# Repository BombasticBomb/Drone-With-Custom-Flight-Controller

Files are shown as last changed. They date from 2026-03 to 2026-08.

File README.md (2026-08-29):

## Custom Drone Flight Controller
Arduino + MPU9250 based Flight Controller for Quadcopter!
This project is a custom-built quadcopter drone that uses an Arduino flight controller with an MPU9250 IMU. Will use a flight controller written in Arduino C++ with a cascaded PID loop for stabilization!

## Build Journal Log
Link: https://github.com/BombasticBomb/Custom-Flight-Controller-Quadcopter-With-RaspberryPI-Cam/blob/main/JOURNAL.md

## 3D Model

This'll be printed in Carbon Fiber Nylon Filament, so it is actually strong enough to be a drone chassis. I will also use a Gyroid infill pattern with 40% infill to make it really strong, and I'll also use a wall count of 6 for further reinforcement. 
parts

## Inspiration
This is my hack club project to build a quadcopter from scratch with a custom flight controller with Arduino &amp; MPU9250. Growing up, I'd watch many science and engineering videos online; I've always been a science kid who spends his time watching astronomy, engineering, etc type videos. I did this project to challenge myself in learning the ins and outs of how a quadcopter actually works, and also to combine my skills in hardware, electronics, and coding to create something unique and not just follow a tutorial.


 ## What Makes This Project Unique
Unlike most custom drones that rely on preprogrammed ready-to-fly flight controllers, my project uses a fully custom flight controller using Arduino & mpu9250 that I had to do a lot of research to actually learn how it works using custom cascaded PID controller loops (and in the future, an extended Kalman filter), and I am working on developing it into a fully functioning firmware. Along with that, I am utilizing a novel method to stream video transmission using a USB camera and the Raspberry Pi using a Python script that uses OpenCV to play video on a web dashboard hosted in Flask and streamed with Flask-socketio. This is a unique method as I offload the low-level control to the Arduino, while I implement advanced features such as a camera (and hopefully in the future GPS, ultrasonic sensors, etc) through the more powerful Raspberry Pi, which actually runs the Linux Operating System.
- Arduino --> Does the low-level flight control and sensor fusion
- Raspberry Pi --> Video Streaming
**Note: Using the onboard wifi on the Raspberry Pi does mean the video transmission range is limited, and beyond that range, we have to rely solely on radio.

## Wiring Diagrams
circuit diagram


| # | Arduino --> MPU9250 | | |
| - | --- | - | --- |
| | **Arduino** | --> | **MPU9250** |
| | 5V | --> | 5V |
| | GND | --> | GND |
| | A4 | --> | SDA |
| | A5 | --> | SCL |

| # | Arduino --> RC Receiver | | |
| - | --- | - | --- |
| | **Arduino** | --> | **RC Receiver** |
| | 5V | --> | 5V |
| | GND | --> | GND |
| | RX | --> | IBus |

| # | Arduino --> ESC | | |
| - | --- | - | --- |
| | **Arduino** | --> | **ESC** |
| | 5V | --> | 5V |
| | GND | --> | GND |
| | 3 | --> | ESC1 |
| | 4 | --> | ESC2 |
| | 5 | --> | ESC3 |
| | 6 | --> | ESC4 |

## Custom PCB:

pcb
Note: The ESCs themselves are part of the wiring diagram and are powered by the Arduino. It is crucial to note the motors themselves, and the Arduino also gets power from the main battery. The reason this configuration was required is that the Arduino converts the 11.1V on the 3S battery to 5V and supplies it to the other electronics.

# Bill of Materials

| Name | Purpose | Quantity | Total Cost (USD) | Link | Distributor |
|---|---|---|---|---|---|
| EVE 50PL 21700 5000mAh 50A Battery | This'll power the drone through its flight. I decided to buy Li-ion batteries and manually connect 3 to make a 3S cell to make a 5000mAh 3S battery pack. This'll help the drone fly longer. I'm buying one extra just in case. | 4 | 24.00 | https://www.18650batterystore.com/products/eve-50pl-21700-5000mah-50a-battery?variant=46405896798359 | 18650 Battery Store |
| JLCPCB Order + Shipping | I'll be manufacturing my custom PCB from JLCPCB. | 1 | 4.30 | https://cart.jlcpcb.com/quote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 | JLCPCB |
| Male & Female Headers | It'll be used to connect things on the PCB. | 1 | 3.82 | https://www.aliexpress.us/item/3256805860047704.html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 | AliExpress |
| XT90 Male to XT60 Female connector for battery | This converts the XT90 on the battery to XT60 so it can be connected to the PCB. | 1 | 1.00 | https://www.aliexpress.us/item/3256809870073827.html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 | AliExpress |
| Drone Frame | This will be the frame that I will be doing all the testing on. I'll have to ship it to my location. | 1 | 5.00 | https://github.com/hackclub/print-legion | Hack Club Legion |
| 1400KV Brushless Motors | These will be the motors that generate lift for the drone. | 4 | 33.40 | https://www.robotshop.com/products/e-s-motor-xxd-a2212-brushless-motor-160w-mounting-base-kits-kv-1400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 | Robotshop |
| Raspberry PI 4 4GB | This will be used to connect the USB camera and for video transmission. I already have this, so I will not need to buy it. | 1 | 0.00 | https://www.centralcomputer.com/raspberry-pi-4-model-b-rpi4-modbp-4gb-4gb-ddr4-ram-bcm2711-soc-usb-3-0-poe-enabled.html | Central Computers |
| Arduino Nano | This will be running the flight software and controlling the motors. I already have this, so I will not need to buy it. | 1 | 0.00 | https://www.aliexpress.us/item/3256809956121978.html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 | AliExpress |
| GY-91 Board with both MPU-9250 & BMP180 | This will the the 9 Axis Flight Controller for the drone (Gyroscope, Accelerometer, Magnetometer, Altometer). | 1 | 6.34 | https://www.aliexpress.us/item/3256810419378175.html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 | AliExpress |
| 8x4.5 Inch RC Drone Propellers | These will be used on the brushless motors to provide lift for the drone. I am buying 8 pieces instead of 4 in case some break during testing. | 1 | 0.92 | https://www.aliexpress.us/item/2251832730802090.html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 | AliExpress |
| 3S Li-po Battery Charger US Plug | This will be used to charge the battery. | 1 | 11.61 | https://www.aliexpress.us/item/3256805934795867.html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 | AliExpress |
| MicroZone MC6C Mini V2 2.4G 6CH Controller Transmitter w/ Receiver | This will be used for the radio communication with the drone. | 1 | 35.24 | https://www.aliexpress.us/item/3256807243819244.html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 | AliExpress |
| 30A Brushless Motor ESC | This will be the Electronic Speed Controller for the 4 brushless motors on the drone. I need to buy 2 pieces for a total of 4 for each motor. | 1 | 12.87 | https://www.aliexpress.us/item/2252799818726193.html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 | AliExpress |
| 12V-5V Buck Converter | This'll convert the 11.1V from the 21700 battery pack to 5V so the Raspberry PI can use it. | 1 | 0.99 | https://www.aliexpress.us/item/3256806059787124.html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 | AliExpress |
| **Total** | | | **139.49** | | |

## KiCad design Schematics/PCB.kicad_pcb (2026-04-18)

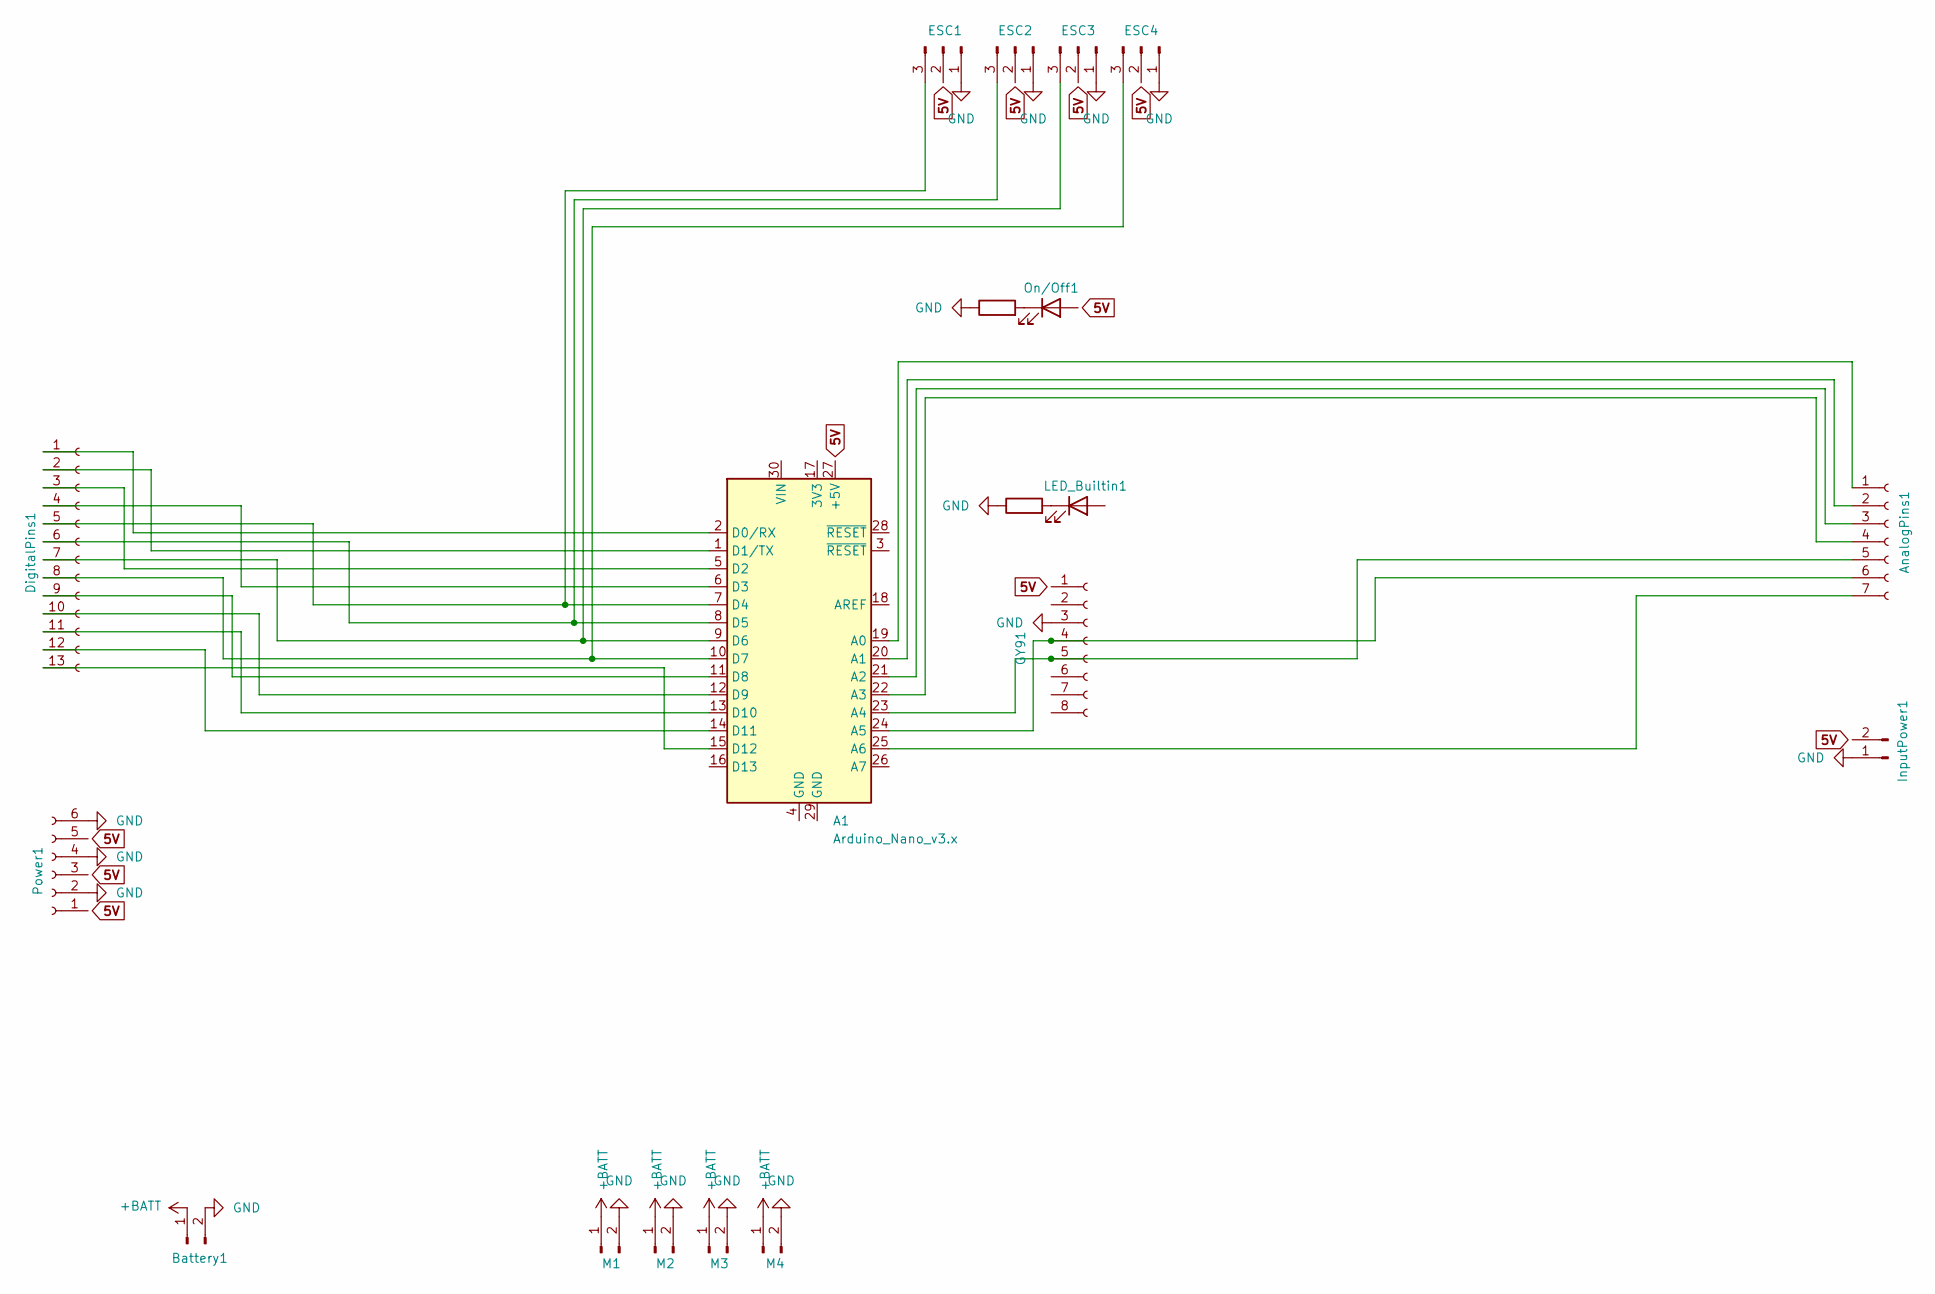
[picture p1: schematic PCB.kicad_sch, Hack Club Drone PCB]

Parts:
A1: Arduino_Nano_v3.x; Arduino_Nano
AnalogPins1: Conn_01x07_Socket; PinSocket_1x07_P2.54mm_Vertical
Battery1: Conn_01x02_Pin; AMASS_XT60PW-M_1x02_P7.20mm_Horizontal
DigitalPins1: Conn_01x13_Socket; PinSocket_1x13_P2.54mm_Vertical
ESC1, ESC2, ESC3, ESC4: Conn_01x03_Pin; PinSocket_1x03_P2.54mm_Vertical
GY91: Conn_01x08_Socket; PinSocket_1x08_P2.54mm_Vertical
InputPower1: Conn_01x02_Pin; PinSocket_1x02_P2.54mm_Vertical
LED_Builtin1: LED; LED_D5.0mm
M1, M2, M3, M4: Conn_01x02_Pin; AMASS_XT60PW-M_1x02_P7.20mm_Horizontal
On/Off1: ON/OFF; LED_D5.0mm
Power1: Conn_01x06_Socket; PinSocket_1x06_P2.54mm_Vertical
R220-1, R220-2: 220; R_Axial_DIN0207_L6.3mm_D2.5mm_P10.16mm_Horizontal

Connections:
+BATT: Battery1.1, M1.1, M2.1, M3.1, M4.1
GND: Battery1.2, ESC1.1, ESC2.1, ESC3.1, ESC4.1, GY91.3, InputPower1.1, M1.2, M2.2, M3.2, M4.2, Power1.2, Power1.4, Power1.6, R220-1.1, R220-2.1
unnamed: A1.19 (A0), AnalogPins1.1
unnamed: A1.20 (A1), AnalogPins1.2
unnamed: A1.21 (A2), AnalogPins1.3
unnamed: A1.22 (A3), AnalogPins1.4
unnamed: A1.23 (A4), AnalogPins1.5, GY91.5
unnamed: A1.24 (A5), AnalogPins1.6, GY91.4
unnamed: A1.25 (A6), AnalogPins1.7
unnamed: A1.2 (D0/RX), DigitalPins1.1
unnamed: A1.1 (D1/TX), DigitalPins1.2
unnamed: A1.5 (D2), DigitalPins1.3
unnamed: A1.6 (D3), DigitalPins1.4
unnamed: A1.7 (D4), DigitalPins1.5, ESC1.3
unnamed: A1.8 (D5), DigitalPins1.6, ESC2.3
unnamed: A1.9 (D6), DigitalPins1.7, ESC3.3
unnamed: A1.10 (D7), DigitalPins1.8, ESC4.3
unnamed: A1.11 (D8), DigitalPins1.9
unnamed: A1.12 (D9), DigitalPins1.10
unnamed: A1.13 (D10), DigitalPins1.11
unnamed: A1.14 (D11), DigitalPins1.12
unnamed: A1.15 (D12), DigitalPins1.13
unnamed: LED_Builtin1.1 (K), R220-2.2
unnamed: On/Off1.1 (K), R220-1.2

Board: 2 copper layers, 19 parts (0 on the bottom side), 24 nets, no tracks yet.

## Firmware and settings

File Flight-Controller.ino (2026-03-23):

// NOTE:
// This is early-stage development of the flight controller.
// Due to lack of physical hardware testing, motor control and PID tuning
// are not finalized yet. Current functionality just focuses on sensor fusion from a mpu6050 which I own for testing purposes, and will switch to a mpu9250 when I get to buy the actual sensor.
// It's the concept and engineering method that is being laid down right now, and it may change or be reimplemented as I build the drone.


#include <SPI.h>
#include <Wire.h>
#include <MPU6050.h>

//MPU
MPU6050 mpu; //I am using mpu6050 cause I have that with me so I can test with it. After I recieve my mpu9250, I'll update the code to use that. 

bool initialized = false;

// Timing
unsigned long prevTime = 0;
unsigned long lastDisplay = 0;

// Angles
float roll = 0;
float pitch = 0;
float yaw = 0;

// Accel angles
float accel_roll = 0;
float accel_pitch = 0;

//Motor libraries
#include <Servo.h>
#include <IBusBM.h>

//Define 4 motors
Servo motor1;
Servo motor2;
Servo motor3;
Servo motor4;

//Define bus for radio communication
IBusBM iBus;

//Flight state
bool flight = false;
int motor1_speed = 0;
int motor2_speed = 0;
int motor3_speed = 0;
int motor4_speed = 0;

void setup() {
  Serial.begin(115200);

  while (!mpu.begin(MPU6050_SCALE_2000DPS, MPU6050_RANGE_8G)) { //2000 degrees and 8G
    Serial.println("Sensor not found!");
    delay(500);
  }
  mpu.setDLPFMode(MPU6050_DLPF_4); 

  // Gyro calibration
  mpu.calibrateGyro();
  mpu.setThreshold(0);

  prevTime = millis();

  iBus.begin(Serial);
  
  //Connect wires (pin 3,4,5,6)
  motor1.attach(3);
  motor2.attach(4);
  motor3.attach(5);
  motor4.attach(6);

  //Ground drone
  ground();
  
  //Wait 3 seconds for initialization
  delay(3000);
}

void loop() {
  unsigned long now = millis();
  float dt = (now - prevTime) / 1000.0;
  prevTime = now;

  // Read sensors
  Vector gyro = mpu.readNormalizeGyro();
  Vector accel = mpu.readNormalizeAccel();

  // Compute accel angles
  accel_roll = atan2(accel.YAxis, accel.ZAxis) * 180.0 / M_PI;
  accel_pitch = -atan2(accel.XAxis, sqrt(accel.YAxis * accel.YAxis + accel.ZAxis * accel.ZAxis)) * 180.0 / M_PI;

  // Initialize
  if (!initialized) {
    roll = accel_roll;
    pitch = accel_pitch;
    yaw = 0;
    initialized = true;
  } 
  
  else {
    float alpha = 0.98;

    //sensor fusion
    roll = alpha * (roll + gyro.XAxis * dt) + (1 - alpha) * accel_roll;
    pitch = alpha * (pitch + gyro.YAxis * dt) + (1 - alpha) * accel_pitch;

    //Yaw
    yaw += gyro.ZAxis * dt;
  }

  /*
    -If the stick is at the very bottom: The value will be ~1000.
    -If the stick is halfway up: The value will be ~1500.
    -If the stick is at the very top: The value will be ~2000.
  */
  //I am guessing this information based on the internet, but the truth will unveil when I actually test the reciever and transmitter
  int altitude = iBus.readChannel(2);
  int rotation = iBus.readChannel(3);
  int lr = iBus.readChannel(0);
  int fb = iBus.readChannel(1);

  

  //Up and down
  //=========================================================================
  if(abs(altitude - 1500) < 10){
    if(!flight){
      ground();
    }
    else{
      //This is when drone is stable in the air
      stabilize(roll, pitch, gyro, dt, motor1_speed, motor2_speed, motor3_speed, motor4_speed);
    }
  }
  
  else{
    if(altitude >= 1510){
      motor1_speed = map(altitude, 1510, 2000, 50, 100);
      motor2_speed = map(altitude, 1510, 2000, 50, 100);
      motor3_speed = map(altitude, 1510, 2000, 50, 100);
      motor4_speed = map(altitude, 1510, 2000, 50, 100);
      update_speed();

      //Toggle flight mode
      flight = true;
    }
    if(altitude <= 1490){
      if(flight){
        motor1_speed = map(altitude, 1000, 1490, 0, 50);
        motor2_speed = map(altitude, 1000, 1490, 0, 50);
        motor3_speed = map(altitude, 1000, 1490, 0, 50);
        motor4_speed = map(altitude, 1000, 1490, 0, 50);
        update_speed(); 
      }
    }
    else{
      return;
    }
  }
  //=========================================================================


  //Rotation
  //=========================================================================
  if(rotation > 1500){
    //***20% increase/decrease for rotation
    motor1_speed += 20;
    motor2_speed -= 20;
    motor3_speed += 20;
    motor4_speed -= 20;
    update_speed();
  }
  if(rotation < 1500){
    motor1_speed -= 20;
    motor2_speed += 20;
    motor3_speed -= 20;
    motor4_speed += 20;
    update_speed();
  }
  //=========================================================================

  //Left/Right
  //=========================================================================
  if(lr > 1500){
    //***20% increase/decrease for left/right
    motor1_speed -= 20;
    motor2_speed -= 20;
    motor3_speed += 20;
    motor4_speed += 20;
    update_speed();
  }
  if(lr < 1500){
    motor1_speed += 20;
    motor2_speed += 20;
    motor3_speed -= 20;
    motor4_speed -= 20;
    update_speed();
  }
  //=========================================================================

  //Front/Back
  //=========================================================================
  if(fb > 1500){
    //***20% increase/decrease for front/back
    motor1_speed -= 20;
    motor2_speed += 20;
    motor3_speed += 20;
    motor4_speed -= 20;
    update_speed();
  }
  if(fb < 1500){
    motor1_speed += 20;
    motor2_speed -= 20;
    motor3_speed -= 20;
    motor4_speed += 20;
    update_speed();
  }
  //=========================================================================

  //Check for speed to ground
  if(motor1_speed <= 10 || motor2_speed <= 10 || motor3_speed <= 10 || motor4_speed <= 10){
    ground();
    flight = false;
  }

}

//Stabilizing function
void stabilize(float roll, float pitch, Vector gyro, float dt, int &motor1_speed, int &motor2_speed, int &motor3_speed, int &motor4_speed) {
  //This is a basic stabilize loop to control the drone while in stabilization

  
  //PID constants, tune later after physically building the drones
  float Kp = 1.5;
  float Ki = 0.0;
  float Kd = 0.5;

  //0* for stability
  float target_roll = 0;
  float target_pitch = 0;

  
  float integral_roll = 0;
  float integral_pitch = 0;

  float prev_error_roll = 0;
  float prev_error_pitch = 0;

  float error_roll = target_roll - roll;
  float error_pitch = target_pitch - pitch;

  //Integrate
  integral_roll += error_roll * dt;
  integral_pitch += error_pitch * dt;


  //Derivative
  float d_roll = -gyro.XAxis;
  float d_pitch = -gyro.YAxis;

  //PID = P + I + D
  float roll_output  = Kp * error_roll  + Ki * integral_roll  + Kd * d_roll;
  float pitch_output = Kp * error_pitch + Ki * integral_pitch + Kd * d_pitch;

  //Motor output
  motor1_speed = motor1_speed - roll_output + pitch_output;
  motor2_speed = motor2_speed + roll_output + pitch_output;
  motor3_speed = motor3_speed + roll_output - pitch_output;
  motor4_speed = motor4_speed - roll_output - pitch_output;

  //control it to 100%
  motor1_speed = constrain(motor1_speed, 0, 100);
  motor2_speed = constrain(motor2_speed, 0, 100);
  motor3_speed = constrain(motor3_speed, 0, 100);
  motor4_speed = constrain(motor4_speed, 0, 100);

  //Update motors
  update_speed();
}


//Set speed of the motors
void set_speed(Servo &motor, int throttle){
  int ms = map(throttle, 0, 100, 1000, 2000);
  motor.writeMicroseconds(ms);
  delay(5);
}

//Ground drone
void ground(){
  motor1.writeMicroseconds(1000);
  motor2.writeMicroseconds(1000);
  motor3.writeMicroseconds(1000);
  motor4.writeMicroseconds(1000);
}

void update_speed(){
  set_speed(motor1, motor1_speed);
  set_speed(motor2, motor2_speed);
  set_speed(motor3, motor3_speed);
  set_speed(motor4, motor4_speed);
}

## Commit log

2026-03-22 Revise BOM format and add new components
    Updated the Bill of Materials (BOM) section with new format and additional parts, including descriptions and links.
2026-03-23 Update pin mappings for ESC connections in README
2026-03-23 updated bom
    [Custom Flight Controller Quadcopter-bom.csv]
2026-04-18 Updated PCB
    [PCB-B_Cu.gbr, PCB-B_Mask.gbr, PCB-B_Paste.gbr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]
